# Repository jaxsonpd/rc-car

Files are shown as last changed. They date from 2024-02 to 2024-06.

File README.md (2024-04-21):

Wacky Racers
===============

This contains a directory structure for your assignment.

doc -- documentation

hw  -- hardware (add your schematic PDF here)

src -- source code

Assignment instructions
-----------------------

The [instructions](https://eng-git.canterbury.ac.nz/wacky-racers/wacky-racers/-/raw/master/doc/instructions/instructions.pdf) are in a PDF file stored in this repository (you'll also get a copy when you fork the project).

Assignment guide
----------------

The [guide](https://eng-git.canterbury.ac.nz/wacky-racers/wacky-racers/-/raw/master/doc/guide/guide.pdf) is a PDF file stored in this repository (you'll also get a copy when you fork the project).

C style Guide
-------------

https://github.com/jaxsonpd/etc/blob/main/Guides/C%20Style%20Guide.md

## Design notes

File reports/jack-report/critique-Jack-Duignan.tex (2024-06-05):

\documentclass[a4paper,12pt]{article}
\usepackage{color}

\setlength{\oddsidemargin}{0mm}
\setlength{\evensidemargin}{-14mm}
\setlength{\marginparwidth}{0cm}
\setlength{\marginparsep}{0cm}
\setlength{\topmargin}{2mm}
\setlength{\headheight}{0mm}
\setlength{\headsep}{0cm}
\setlength{\textheight}{240mm}
\setlength{\textwidth}{168mm}
\setlength{\topskip}{0mm}
\setlength{\footskip}{10mm}
\setlength{\parindent}{8ex}

\newcommand{\comment}[1]{\emph{\color{blue}#1}}

\title{ENCE461 Wacky Racers Assignment Critique}
\author{Jack Duignan, Group 33, Hat board}
\date{\today}

\begin{document}
\maketitle

\section{Strengths}

The group 33 wacky hat had three main strengths. First the design of the PCB was very clean with a large number of test-points and no components on the back. This allowed for quick assembly and easy debugging. Second, the board had the ability to be powered from both battery and USB. This was achieved using a header which could be bridged to bypass the H-bridge and supply VBUS directly to the 5V plane. This was extremely useful allowing for testing of the radio without a battery. Third, the software was modularised and well documented allowing both the members of the hat and the car to work on each others problems without much verbal explanation needed.

\section{Weaknesses}

The wacky hat had three weaknesses. First the buzzer was powered off 3V3 without a resister in parallel. This meant that the sound produced was quiet making the song hard to hear. Second, the linear voltage regulators had their bypass pins pulled high which stopped them working correctly luckily these could be pried up from the PCB and the fault was rectified without needing to replace any components. Third the sensitivity of the control system, specifically of the y-axis (turning), was very high making the racer hard to control at slow speeds. This was fixed somewhat in the lead up to the race; however the control system value calculation should have been completely rewritten.

\section{Improvements}

The hat could be improved by: powering the buzzer off 5V with a resistor in series, leaving the 3V3 linear regulators bypass pins floating, and by implementing more gradual sensitivity on the y-axis. These improvements are small things that did not affect the core functionally of the system and where easily rectified. As a whole the system performed well without bugs.

\section{Contribution}

I had four main contributions to the project. First, I created the base schematic used for both the wacky hat and racer which included the SAM4S and radio, GPIO and power supplies. Second, I completed around half of the PCB tracing and layout for the wacky hat. Third I wrote the majority of the software for the wacky hat including the main scheduler, accelerometer interfacing, and the buzzer code. Fourth I completed some debugging of the wacky racer including radio communication and scheduling. I think my contribution was more than others in the team but this was a reflection of the greater amount of spare time that I had when the milestones were due.

\section{Recommendations for future students}

My main recommendation is to start early and leave a large amount of time for the PCB as this is crucial to get right. My team spent a long time on the PCB and schematic design and because of this had to do functionally no rework making the rest of the project much easier. Secondly I would encourage other students to read through the provided libraries as they contain a lot of great examples of well written code and give a good starting point for the software. Finally I would recommend that students design the system with the race in mind with tuning parameters that can be used to change how the controller handles as this will give them a huge advantage in the race.

\section{Recommendations to improve project}

I think that another milestone should be added after radio communication which assess the performance of the racer-hat system. Then the race should be pushed to study leave or everything moved a week forward in the term. I also think that it is imperative that more lab slots are added on another day with the ability for students to ask questions on the first day then be assessed on the second. This is nessasary as the current system does not really allow for any of the actual software design to be completed in the labs. Finally I think that more time needed to be allowed during software development to ensure that the students create clean code that is well modularised. 

\section{Peer assessment}

\noindent
\begin{tabular}{|l|l||l|l|}
\hline
\multicolumn{2}{|c||}{My board} & \multicolumn{2}{c|}{Whole system} \\
\hline
Name \hspace{5cm} & Score     & Name \hspace{5cm} & Score \\
\hline \hline
Jack Duignan        & 3 & Jack Duignan        &  3 \\ \hline
Ethan Wildash-Chan  & 2 & Ethan Wildash-Chan  &  2 \\ \hline
                    & & Isha Patel            &  2 \\ \cline{3-4}
                    & & Daniel Hawes          &  3 \\ \hline
\end{tabular}

\section{Workload}

\noindent
\begin{tabular}
  {|l|l|l|l||
    l|l|l|l||
    l|l|l|l|}
  \hline
  \multicolumn{4}{|c||}{Racer} &
  \multicolumn{4}{|c||}{Hat} &
  \multicolumn{4}{|c|}{System integration}  \\ \hline
    Des & Bld & SW & Test &
    Des & Bld & SW & Test &
    Des & Bld & SW & Test \\ \hline
    4 & 1 & 4 & 4 &
    37 & 7 & 45 & 10 &
    1 & 0 & 10 & 15 \\ \hline
\end{tabular}
\end{document}

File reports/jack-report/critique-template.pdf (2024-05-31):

# ENCE461 Wacky Racers Assignment Critique

### Jack Duignan, Group 33, Hat board

### May 31, 2024

## 1 Strengths

In this section describe what you think are the strengths of your design, PCB layout, and overall wacky racer are.
The group 33 wacky hat had three main strengths. First the design of the PCB was very clean with a large number of testpoints and no components on the back. This allowed for quick assembly and easy debugging as the traces visable. Second, the board had the ability to be powered from both battery and USB. This was achived using a header which could be bridged to bypass the H-bridge and supply VBUS directly to the 5V plane. This was extremly useful allowing for testing of the radio without a battery. Third, the software was modularesed and well documented allowing both the hat and car to work on each others problems without explination needed. This simplified debugging.

## 2 Weaknesses

In this section describe what you think are the weaknesses of your design, PCB layout, and overall wacky racer are.
The wacky hat had three weaknesses. First the buzzer was powered off the 3V3 without a resister in parallel. This meant that the sound produced was quiet and in the end a resistor was soldered across the buzzer terminals. Second, the linear voltage regulators had there bypass pins pulled high which stopped this working luckly these could be pried up from the PCB and the fault was rectified without needing to replace any components. Third the control system spesifically the sensitivity of the y-axis (turning) was very high making the racer hard to control at slow speeds this was mitigated somewhat; however more needed to be done.

## 3 Improvements

In this section describe what you would like to have done differently with the advantage of hind-sight.
The hat could be improved by: powering the buzzer off 5V with a resistor in series, leaving the 3V3 linear regulators bypass pins floating, and by implementing more gradual sensitivity on the y-axis.

## 4 Contribution

In this section describe what you perceive as your contribution to the project compared to the other members of your team.
I had four main contributions to the project. First, I created the base sechematic used for both the wacky hat and racer which included the SAM4S and radio, GPIO and power supplies. Second, I completed around half of the PCB tracing and layout for the wacky hat. Third I wrote the majority of the software for the wacky hat including the main schedular, acceleromiter interfacing, and the buzzer code. Fourth I completed some debugging of the wacky racer including radio comunication and scheduling.

## 5 Recommendations for future students

In this section describe recommendations (with reasons) for future students doing a similar project.
The main recommendation is to start early and leave a large amount of time for the PCB as this is cricual to get right. My team spent a long time on the PCB and schematic design and becouse of that had to do functionally no rework making the rest of the project much easier. Secondly I would incouge other students to read through the provided libraries as they contain a lot of great examples of well writen code and give a good starting point for the software. Finally I would recommend that students design the system with the race in mind with tunning paramiters that can be used to change how the controller handles. As this give them a huge advantage in the race.

## 6 Recommendations to improve project

In this section describe your recommendations (with reasons) for how the project could be improved.
I think that another milestone should be added after radio communication which assess the performance of the racer, hat system. Then the race should be pushed to study leave or everything moved a week forward. Second I think that it is imperitive that more lab slots are added on another day with the ability for students to ask questions of the first day then be assessed on the second. This is nessasary as the current system does not really allow for any of the actual software design to be completed in the labs.

## 7 Peer assessment

There are two assessments to fill into the table:
My board | Whole system
Name | Score | Name | Score
Jack Duignan | 3 | Jack Duignan | 3
Ethan Wildash-Chan | 2 | Ethan Wildash-Chan | 2
| | Isha Patel | 2
| | Daniel Hawes | 3

## 8 Workload

Racer | Hat | System integration
Des | Bld | SW | Test | Des | Bld | SW | Test | Des | Bld | SW | Test
4 | 1 | 4 | 4 | 37 | 7 | 45 | 10 | 1 | 0 | 10 | 15

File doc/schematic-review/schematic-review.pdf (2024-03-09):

# ENCE461 Schematic Review

### M.P. Hayes

Bring your schematics, printed on A3 paper

## 1 Common

1. Student names and group number in title block
2. Battery fusing (this is mandatory)
3. Use serial wire debug interface for programming
4. 3.3 V MCU regulator can be back driven (the CAT6219 can). Others may require a diode
5. Short circuit protection for MCU pio pins going to external headers
6. Battery voltage monitoring
7. The analogue inputs to the MCU do not exceed 3.3 V
8. LEDs for debugging
9. Jumpers for mode configuration (radio channel select)
10. Test points
11. Ground test points
12. USB signals are not swapped
13. USB has series termination resistors (27 ohm)
14. Power supply filtering for radio (recommend ferrite bead or resistor in series with power rail with parallel capacitor)
15. The radio needs to be connected to SPI pins (MISO/PA12, MOSI/PA13, SCK/PA14)
16. Radio IRQ connected to MCU PIO pin
17. Radio uses SPI clock (SCK) not the TWI clock (TWCK)
18. TWI uses TWCK0/PA4 and TWD0/PA3 or TWCK1/PB5 and TWD1/PB4.
19. SAM4S erase pin on testpoint
20. SAM4S has 12 MHz crystal

1

21. Reset button connected to NRST pin
22. Power on/off button connected to WKUPn pin
23. Avoid PB4–PB5 for general I/O (they default to JTAG pins on reset but can be reconfigured in software)
24. Have external pull-down resistors to ensure chips are disabled on power-up
25. Have a few spare PIO pins connected to pads for last minute mods.

## 2 Hat board

1. Drive circuit for piezo tweeter
2. Accelerometer nCS pin connected high to enable I2C operation
3. Pullup resistors on TWI (I2C) bus

## 3 Racer board

1. Can isolate H-bridge and buck regulator with jumper or zero ohm resistors
2. MOSFET(s) for actuator (if use p-channel MOSFET need transistor to provide sufficient gate voltage to turn MOSFET off)
3. H-bridge driven by four PWM signals (it is best to use PWMHx, note PWMLx and PWMHx are complementary)
4. H-bridge AISEN and BISEN pins connected to ground (unless using current control)

2

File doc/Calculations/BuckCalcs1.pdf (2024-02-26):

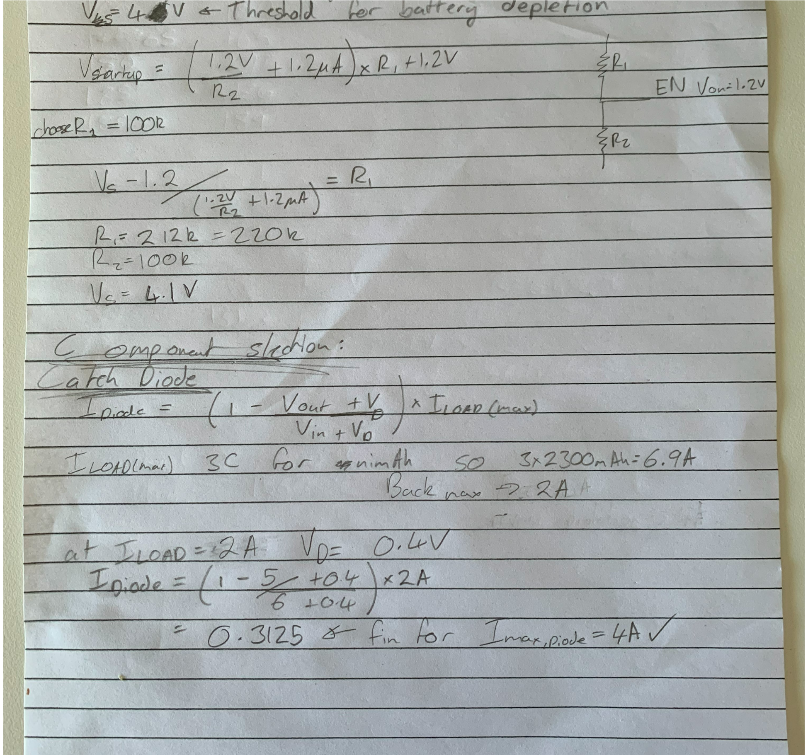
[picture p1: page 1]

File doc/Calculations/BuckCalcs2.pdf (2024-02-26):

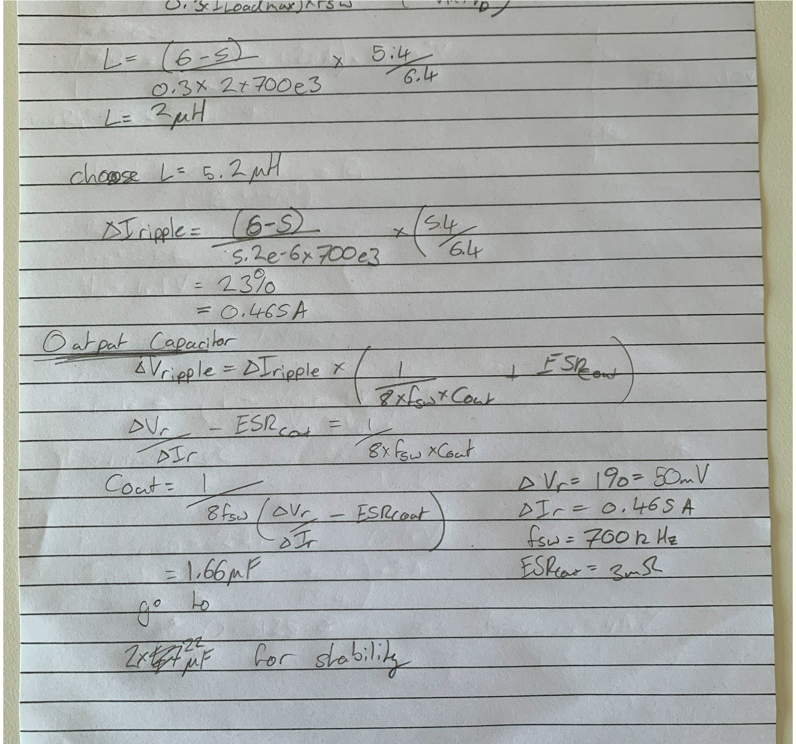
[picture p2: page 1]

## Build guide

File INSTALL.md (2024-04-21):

# Install

This document details the installation process for the toolchain on wsl

# Installing WSL

Source: https://learn.microsoft.com/en-us/windows/wsl/install

Open a powershell prompt as an admimastrator and run:

```
wsl --install
```
This installs ubuntu.

Restart the terminal and now ubuntu should be in the drop down. Let it install then set user name and password.

Once this is completed you can then ensure it is up to date using:

```
sudo apt update && sudo apt upgrade
```

# USB pass through

Source: https://learn.microsoft.com/en-us/windows/wsl/connect-usb

1. Install usbipd (download the msi)
2. Attach usb device to the windows machine
3. Run 
```
usbipd list
```
to list comands
4. bind the usb device that should be shared (this makes it available to wsl)
```
usbipd bind --busid 4-4
```
5. Attach the usb device to wsl
```
usbipd attach --wsl --busid <busid>
```
6. Then use:
```
lsusb
```
To list the devices attached to the ubuntu installation

# Toolchain

The toolchain can then be downloaded using the guide found at:

https://eng-git.canterbury.ac.nz/wacky-racers/wacky-racers/-/raw/master/doc/guide/guide.pdf?inline=true

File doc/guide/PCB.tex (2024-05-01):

\chapter{PCB layout}

Before you lay out your PCB, an hour spent checking your schematic
will avoid many hours of testing and rework grief!  I annotate a
printed schematic with a highlighter to ensure I have considered
everything.

Laying out a PCB is a topological puzzle.  Note only do you need to
connect all the components, you need to consider:
%
\begin{enumerate}
\item Signal integrity

\item Manufacturability

\item Testability

\item Thermal issues
\end{enumerate}

\section{Altium tutorial}

The Altium tutorial for creating a PCB can be found on the ENCE461
Learn page.

\label{pcb-recommendations}

\section{Placement}
\label{placement}

\begin{enumerate}
\item
  Keep small signal analogue components (radio) well away from digital
  electronics and power electronics.
\item
  Place local decoupling capacitors close to MCU to minimise the loop area.
\item
  Place bulk capacitors close to where power comes from.
\item
  Keep the crystal close to the MCU.
\item
  Place switches so they can be pushed.
\item
  Place LEDs so they can be seen.
\item
  Place USB connector so it can be connected to.
\item
  Place connectors on edge of PCB with wires going away from the board.
\end{enumerate}

\section{Power supplies}

The goal of routing power supplies is to reduce impedance (both
resistive and inductive).

\begin{enumerate}

\item Use planes for power distribution.

\item Use separate vias for every power and ground connection.

\item If cannot use power plane for power connection, make trace as
  wide\footnote{To reduce inductance and resistance.} as possible.

\item Do not put splits in planes\footnote{Unless you know what you
  are doing.}.

\item Keep planes away from the radio antenna; otherwise the radio
  range is limited.

\item Before `pouring' a polygon to create a power or ground plane
  connect the nets with traces and vias.
\end{enumerate}

\section{Signal traces}

The goal of routing signal traces is to reduce crosstalk to improve
signal integrity.  You should always consider the return current path;
this will take the path of least impedance.

% https://resources.altium.com/p/differential-pair-impedance-using-calculator-design-your-pcb

% https://resources.altium.com/p/differential-microstrip-impedance-calculator

\begin{enumerate}

\item First, route differential signal traces as a pair (e.g., USB) on
  top layer (to form microstrips with the ground
  plane)\footnote{Ideally, the differential characteristic impedance
    should be 90 ohms.  This depends on the trace width, trace
    separation, trace thickness, and height of the traces above the
    ground plane.  If you are keen see \url{
 https://resources.altium.com/p/differential-microstrip-impedance-calculator}.}.

\item Route high-speed (above 50\,kHz, e.g., SPI, I2C) signal traces
  on the top layer (to form a microstrip with the ground plane).
  These traces can be thin\footnote{The trace width affects the
    characteristic impedance of the microstrip but this is not an
    issue for the small boards used for the assignment.}, say
  0.3\,mm\footnote{The manufacturer can produce 0.15\,mm traces but
    the Altium design rules for this assignment set a minimum width of
    0.2\,mm to be safe.}.

\item Keep a high-speed trace well away from any other trace to reduce
  crosstalk (see the 3-W rule).

\item Avoid high-speed signal traces jumping layers\footnote{This
  makes the return current take a tortuous path, increasing
  crosstalk.}.  If you have to, use vias close to the ends of traces
  and run the traces on the bottom layer (to form a microstrip with
  the power plane).  Be careful not to route traces on the bottom
  layer over gaps in the power plane (this breaks the microstrip and
  thus increases crosstalk) \footnote{See \url{https://www.signalintegrityjournal.com/articles/692-split-planes-and-what-happens-when-microstrip-signals-cross-them}.}.

\item Route low-level analogue signals well away from the high-speed
  traces, preferably on the bottom layer (where they are shielded from
  the high-speed traces).

\item Use thick, short traces for high current signals (e.g., motor)
  to reduce resistance.

\item Finally, route the low-speed signal traces (for LEDs and buttons
  etc.).  These can jump layers to go around the high-speed traces.

\end{enumerate}

In the past it was undesirable to have acute angles ($<90^{\circ}$) in
traces due prevent the formation of acid traps during etching.
However, it seems that modern PCB etching does not have this
problem\footnote{\url{https://resources.pcb.cadence.com/blog/are-acid-traps-still-a-problem-for-pcbs-in-2019-2}}.

\section{Vias}

\begin{enumerate}
\item Use normal vias but not blind or buried vias.  The smallest via
  that can be made for this assignment has a 0.3\,mm hole with a
  0.8\,mm annulus.  However, it is better to use a via with a 0.5\,mm
  hole and 1.0\,mm annulus.

\item If you use a via underneath a component with a metal heatsink
  pad, ensure it is tented (these have a layer of insulating solder
  resist).  Note, untented vias are useful for test points.
\end{enumerate}

\section{Recommended layouts}

For any switching power supply, sensitive analogue, or BGA fanout, the
chip manufacturer usually provides a recommended layout.

\section{Check list}
\label{PCB-check-list}

\begin{enumerate}
\item Check your schematic.  Then get someone else to check your
  schematic.  Query every component.

\item Perform a DRC (Design Rule Check)] using Altium.

\item Add PCB test points, test points, and more test points.  You
  will need one for every signal and power supply.  \textbf{You have
    been warned!}  If you don't believe me, compare the size of an
  oscilloscope probe to a surface mount IC pin and see if you can hold
  the probe in place.  I recommend using 1206 test points since the
  smaller ones rip off easily.

    

\item Label the test points on the silk screen with meaningful names.

\item Add ground test points that you can clip an oscilloscope ground
  lead to.  Keep these away from other test points to avoid shorting
  with the oscilloscope ground clip.  I recommend making a
  staple-shaped wire loop, soldered between two holes.



\item Check mounting holes.

\item Check component footprints, especially connectors, voltage
  regulators, and surface mount transistors by placing the parts on a
  print-out of the PCB design.

\item Ensure that power supply traces are wide as possible, preferably
  planes, to reduce their inductance.

\item Ensure that high current traces are wide as possible to reduce
  their resistance.

\item Do not connect IC pins directly between the pads since it is not
  possible to tell if a solder blob is accidental or deliberate.

\item Insert vias to ground plane to ensure that all parts are
  connected.  Do not leave unconnected copper.

%\item If not using plated through vias do not place vias under
%  components.

\item If placing vias under components with exposed metal pads, make
  sure the vias are ``tented'' (covered in solder mask) to prevent
  unexpected shorts.

\item Stitch power or ground planes where vias or traces cut them up.

\item Traces of width $W$ should be separated by at least $2W$ to
  reduce crosstalk.  This is the 3-W rule since the trace centres are
  $3W$.  An exception is for differential signals; these should be
  routed close together with a uniform spacing.

\item Do not run a microstrip traces right on the edge of the PCB.  If
  trace is of width $W$ it should be at least a distance $W$ from the
  edge to reduce electric field fringing effects.

\item Use large traces for pads on connectors that may be subject to
  mechanical forces (power jacks, pluggable terminals, etc.) to
  prevent trace cracking.

\item If you have high voltages check clearances.

\item Check pad to trace clearances to avoid potential solder bridges.

% \item Check that it is possible to top-solder through-hole components
%  on non-plated-through boards.

\item Ensure like signals are grouped, data lines, address lines, control lines, analogue signals, etc.

\item Check the thermal path for parts that get hot.

\item Run traces over reference (power or ground) planes to create a
  microstrip trace; avoid traces running over cuts in a reference
  plane.

\item Check that hole diameters are larger than the pin diameters for
  connectors and through hole. 25\% over the lead diameters is
  typical.  Remember to look at the diagonal dimension for square pins
  or your holes may be too small.

\item Check the drill file report to make sure the hole sizes are what
  you would expect. There should be no holes with sizes of zero, no
  weird sizes, no super large sizes unless required by the design.

\item Check that connections of thermal vias have clearance to other
  traces and pads.

\item Pay close attention to clearances on internal planes of
  multilayer boards; shorts on these planes can only be removed with
  precision drilling.

\item Number pins on connectors, big ICs, selection jumpers, etc. For
  connectors, number enough pins so that the pin ordering is
  obvious.  For large ICs consider adding tickmarks every 5 pins.

\item Make the pad for pin 1 of every IC square. Also consider putting
  a silkscreen dot next to pin 1.

\item Leave at least 20--50\,mils (0.5--1.3\,mm) clearance between
  components and the edge of the board. This makes it less likely that
  inaccuracies in board fabrication will cause part of a pad to get
  chopped off.

\item Check for component clearances from enclosure including heights.

\item Look at each net individually to ensure that it does not take an
  overly long path around the board. Many layout tools have a
  highlight net feature that makes this a fast process.

\item Do not let the silkscreen overlap pads. Try to avoid having
  silkscreen overlapping via holes or areas of the board that will be
  routed away (large holes, slots, tabs, etc.), since legibility will
  be poor.

% \item If ICs are being soldered with solder paste ensure that there is
%  a solder mask between pads.
 \end{enumerate}

\section{Design rule checks}

This section considers common Altium design rule violations.  For more
information see the Altium wiki.

\subsection{PCB manufacture violations}

You do not want any of these.  If a trace is too thin then etching may
produce a hole in it.  It two traces are too close together, they may
end up joined.

\subsection{PCB assembly violations}

If you want to make thousands of boards, then you want to avoid these
violations.  For a one-off board, they do not matter since you can fix
the faults they may cause with a soldering iron.

\subsubsection{SMD neck-down constraint}

Traces connecting to SMD pads often need to be reduced in thickness to
minimise heat transfer from the SMD pad (unequal PAD temperatures can
lead to component tombstoning or rotation in the oven).  The traces
widths should be a maximum of 50 \% of the width of the pad and should
be of the same size to prevent component movement due to unequal pad
temperatures.  The length of the neck-down can be as short as 0.5\,mm.

This is not so critical for integrated circuits with many pins (except
if a solder mask is not used since solder might flow away from the
pad).

\subsubsection{Silk to solder mask}

Here Altium thinks the silk screen is being printed over a pad; most
manufacturers detect this and delete the offending text.  The downside
is that it might make it hard for you to find a component by name.

\subsubsection{Minimum solder mask sliver constraint}

This occurs with chips having pins that are close together.  It is a
warning that the PCB manufacturer may not be able to make the thin
sliver of solder mask that is applied between pads to reduce the
chances of having a solder blob between the pins.  For a prototype it
is not a concern since the solder blob can be easily removed with a
small soldering iron.

\subsubsection{SMD pad to corner}

This is warning about potential acid traps.  You can ignore
it\footnote{\url{https://resources.pcb.cadence.com/blog/are-acid-traps-still-a-problem-for-pcbs-in-2019-2}}.

\subsection{Signal integrity violations}

These are not showstoppers but are important if you want to sell a
product that meets EMC
regulations\footnote{\url{https://learnemc.com/emc-regulations-and-standards}}.

\subsubsection{SMD pad to plane constraint}

What this means is that you have placed a via to a power or ground
plane too far from a SMD pad.  Simply add another via closer to the
pad.  There is no need to skimp on vias for power supply connections.

This violation indicates you that you are adding unnecessary
inductance by increasing the loop area and thus compromising signal
integrity.

Unfortunately, Altium does not detect when you use a power decoupling
capacitor to mitigate this inductance and thus will report
false-positives.  For some reason, whenever there is a decoupling
capacitor pad between an IC pad and a via to a plane, it cannot
calculate the distance of the trace and reports it as being about
2.3\,m!  So, ignore this error.

The goal is to place the decoupling capacitor to minimise the area of
the loop formed by the current flowing from the capacitor to the IC
power and ground pins.  Multiple vias to power/ground planes should
then be placed on the other side of the capacitor.

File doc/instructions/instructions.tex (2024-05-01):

\documentclass[11pt, a4paper]{article}
\title{Wacky Racers 2024 Instructions}
\author{Michael Hayes}
\date{Version 1.111, \today}

\usepackage[margin=1in]{geometry}
\usepackage{parskip}
\usepackage{float}
\usepackage{todonotes}
\presetkeys{todonotes}{inline}{}
\usepackage{graphicx}
\usepackage[T1]{fontenc}
\usepackage{makecell}
\usepackage[breaklinks=true]{hyperref}
\usepackage{tabularx}
\usepackage{subcaption}
\usepackage{listings}
\usepackage{siunitx}
\usepackage{circuitikz}
\usepackage{tikz}
\usetikzlibrary{arrows}

\newcommand{\code}[1]{\texttt{#1}}

\newcommand{\fredyemail}{\url{mailto:fredy.youssif@canterbury.ac.nz}}
\newcommand{\scottemail}{\url{mailto:scott.lloyd@.canterbury.ac.nz}}
\newcommand{\diegoemail}{\url{mailto:diego.ramirez@canterbury.ac.nz}}

\newcommand{\fredy}{\href{mailto:fredy.youssif@pg.canterbury.ac.nz}{Fredy Youssif}}
\newcommand{\scott}{\href{mailto:scott.lloyd@.canterbury.ac.nz}{Scott Lloyd}}
\newcommand{\diego}{\href{mailto:diego.ramirez@canterbury.ac.nz}{Diego Ramirez}}

\newcommand{\theguide}{\href{https://eng-git.canterbury.ac.nz/wacky-racers/wacky-racers/-/blob/master/doc/guide/guide.pdf}{The Wacky Racers Guide}}

\begin{document}
\maketitle

\section{Introduction}

The purpose of this assignment is to design, build, and program an
embedded system using an ARM microcontroller and surface mount
technology.

The goal for each group of four students is to build a remote
controlled vehicle (the Wacky Racer) and its controller (the Wacky
Hat).  At the conclusion of the assignment there will be a dastardly race!

Each group is comprised of two sub-groups of two students.  One of
these subgroups constructs the Wacky Racer and the other constructs
the Wacky Hat.  You may be asking why is the Wacky Hat called the
Wacky Hat?  Well, a hat that controls a remote vehicle using head
motions is not an ordinary hat!

\section{Requirements}

The following requirements are mandatory if you wish to maximise your
marks.

\subsection{Wacky racer}

\begin{enumerate}
\item The chassis is to be constructed by each group.  These can be 3-D printed,
  constructed from Perspex or wood, etc.  A standard chassis is available from
  the Electronics Lab technician (Diego Ramirez).  The electronics must be
  visible on top of the chassis.  The bumper must be as accessible as the
  the standard chassis.
\item Have a standard working bump sensor (supplied).
\item Locomotion can only use two 6\,V DC motors (supplied).
\item Everything must be powered from a single 5-cell NiMH battery pack (supplied).
\item Use a single four layer printed circuit board of dimension 85\,mm$\times$64\,mm.
\item Use an ARM microcontroller (Atmel SAM4S).
\item Drive the motors using H-bridges (Texas Instruments DRV8833 dual
  H-bridge).
\item Regulate the nominal battery voltage to 5\,V with a buck
  regulator IC (ADP2302ARDZ-50).
\item Be decorated with an LED tape (supplied) controlled by the MCU.
\item Use a USB interface for debugging.
\item Use a serial wire debug interface for MCU programming/debugging.
\item Have adequate battery fusing and reverse polarity protection.
\item Have a pushbutton connected to the MCU to enter and wake from
  low-power mode (optional).
\item Have a red LED to indicate errors.
\item Have a green LED to indicate status.
\item If the battery voltage drops below 5\,V, the red LED should flash and high power draw devices should be disabled.
\item Interface to the Wacky Hat with a Nordic nRF24 SMD radio module
.
%\item Have a mounted RFID card (supplied) that can be read by the Wacky ramps.
\item Have jumpers or switches to select four radio channels.
\item Be humorous.
\end{enumerate}

\hspace{120mm}

Each Wacky Racer can have a dastardly means of hindering another
team's Wacky Racer.  However, you cannot:
%
\begin{itemize}
\item Damage or destroy another Wacky racer (except in the battle royale)
\item Damage the venue
\item Injure a spectator
\item Jam the radio signals
\end{itemize}

\vspace{1cm}

\begin{figure}[h]
    \centering
    \input{racer_top_level.tex}
    \caption{Racer board top level diagram.}
\end{figure}

\vfill\pagebreak

\subsection{Wacky hat}

\begin{enumerate}
\item Construct a Wacky Hat that contains all the electronics.
\item Everything must be powered from a single 5-cell NiMH battery pack (supplied).
\item Have adequate battery fusing and reverse polarity protection.
\item Use a single four layer printed circuit board of dimension 85\,mm$\times$64\,mm.
\item Use an ARM microcontroller (Atmel SAM4S).
\item Regulate the nominal 6\,V battery voltage to 5\,V with a buck
  regulator IC (ADP2302ARDZ-50).
\item Be decorated with an LED tape (supplied) controlled by the MCU.
\item Use an I2C accelerometer (ADXL345) for head motion detection.
\item Use a USB interface for debugging.
\item Use a serial wire debug interface for MCU programming/debugging.
\item Have a pushbutton connected to the MCU to enter and wake from
  low-power mode (optional).
\item If the battery voltage drops below 5\,V, the red LED should flash and high power draw devices should be disabled.
\item Have an active-high red LED to indicate errors.
\item Have an active-high green LED to indicate status.
\item Play sound when the bumper is hit.
\item Interface to the Wacky Racer with a Nordic nRF24 SMD radio module.
\item Have jumpers or switches to select four radio channels.
\item Be humorous.
\end{enumerate}

%\vspace{1cm}

\begin{figure}[h]
  \centering
  \input{hat_top_level.tex}
  \caption{Racer hat top level diagram.}
\end{figure}

\vfill\pagebreak

\section{Assignment schedule}

The planned activities for the timetabled labs in the Embedded Systems
Lab (ESL) are:
%
\begin{flushleft}
  \begin{tabular}{ c l l }
    Week            &  Assistance  &  Assessment \\
    \hline \hline
    T1-1 & Altium tutorial 1 (schematics)  & \\
    T1-2 & Altium help      & \\
    T1-3 & Schematic review & Schematic submission for review (Monday 9am) \\
    T1-4 & Altium tutorial 2 (PCB) &          \\
    T1-5 & Altium help      & PCB submission 1    \\
    T1-6 & Altium help      & PCB submission 2    \\
    \hline
    B-1  & (break)          &                   \\
    B-2  & (break)          &                   \\
    B-3  & (break)          &                   \\
    \hline
    T2-1 & General          &                   \\
    T2-2 & General          & Blinky            \\
    T2-3 & General          & Accelerometer/motors        \\
    T2-4 & General          & Radio control     \\
    T2-5 & General          & Functionality     \\
    T2-6 & Competition      & Competition, critique  \\
  \end{tabular}
\end{flushleft}

Notes:
%
\begin{enumerate}
\item There are two lab streams.  Your group will need to sign up to
  one of the streams.  Choose an odd numbered group for the Wednesday
  1--3 pm stream or an even numbered group for the Wednesday 3--5 pm
  stream.

\item There may be a 6--10 day delay for the PCBs to be manufactured
  from the time of submission.  You will then need to book an assembly
  session in the SMT lab provided you have done the SMT lab induction.

\item Do not underestimate the blinky milestone.  The program is
  trivial; you just have to flash an LED.  However, it requires having
  a functional PCB, a functional toolchain, and the ability to
  download code into the microcontroller's flash memory.

\end{enumerate}

\section{Assessment}

The marks breakdown (max. 0x64) is:
%
\begin{flushleft}
  \begin{tabular}{ll}
    PCB submission & 0--0xa marks\\
    Blinky milestone  & 0x5 marks\\
    Accelerometer/motor milestone  & 0x5 marks\\
    Radio control milestone  & 0x5 marks\\
    Functional assessment & 0--0x14 marks \\
    Board inspection & 0--0x1e marks \\
    Competition & 0--0xa marks \\
    Individual critique & 0--0xf marks \\
  \end{tabular}

\end{flushleft}

\subsection{Milestones}

There are five milestones.  To achieve the associated marks, they must
be demonstrated to a T.A. by the end of the lab for your allotted
stream.  If you need an exception to this, see \fredy\ with a
\emph{very} good reason such as isolating with COVID.  The milestone
requirements are:
%
\begin{description}
\item [Schematic review] Submit your A3 schematic on Learn for
  review.  Lose 10 marks if you miss the submission time.

\item [PCB submission] Submit your PCB design to Learn for
  manufacture.  To encourage early submission there is a sliding scale
  for marks depending on when the PCB is submitted, see table.  After
  week 6, there is a 10 mark penalty per week.  \textbf{NB, a rushed
    PCB design will cause you more grief, more PCB rework, and a lower
    mark for the inspection.}

  It is not possible for me to cover all aspects of PCB design before
  your PCB submission.  I recommend you read the lecture notes for
  power supply decoupling and crosstalk.

  \begin{tabular}{llll}
    Week & Submission day & Cut-off time  & Mark \\ \hline
    5    & Monday       & 1.00 pm & 10 \\
    5    & Tuesday      & 1.00 pm & 9 \\
    5    & Wednesday    & 1.00 pm & 8 \\
    5    & Thursday     & 1.00 pm & 7 \\
    5    & Friday       & 1.00 pm & 6 \\
    6    & Monday       & 1.00 pm & 5 \\
    6    & Tuesday      & 1.00 pm & 4 \\
    6    & Wednesday    & 1.00 pm & 3 \\
    6    & Thursday     & 1.00 pm & 2 \\
    6    & Friday       & 1.00 pm & 1  \\
  \end{tabular}

\item [Blinky] Demonstrate that can blink an LED controlled by the SAM4S.

\item [Accelerometer/motors]
  For the Wacky Hat,
  \begin{itemize}
  \item Demonstrate the output of accelerometer readings to a PC using USB CDC (as provided in the test apps).
  \item Map the accelerometer readings to two duty cycles for variable speed and steering control (forward and backward), and output the result to a PC using USB CDC.
  \end{itemize}

  For the Wacky Racer,
  \begin{itemize}
    \item Demonstrate the operation of the locomotion motors using PWM signals (as provided in the test apps).
    \item Provide variable speed and steering control for the locomotion motors (forward and backward) from a PC using USB CDC. 
    \end{itemize}

\item[Radio control]

  Demonstrate sending commands from the Wacky Hat to the Wacky Racer
  and vice-versa over a radio link.

%  Demonstrate sending commands from the Wacky Hat to the Wacky Racer
%  over a radio link.
\end{description}

\textbf{If you cannot show the functionality of a previous milestone
  during any assessment, you will fail that assessment and lose any
  marks from the previous milestone.}

\subsection{Functionality assessment}

Functionality requirements:
%
\begin{flushleft}
  \begin{tabular}{l|l}
    Wacky racer & Wacky hat \\ \hline \hline
    Blink LED                      & Blink LED \\
    Drives LED tape                & Drives LED tape \\
    Drive motors forward/backward  & Read from accelerometer \\
    Speed control of motors        & Determine speed from accelerometer \\
    Steering control               & Determine steering from accelerometer\\
    Receive/send radio message     & Receive/send radio message \\
    Jumper selectable radio channel & Jumper selectable radio channel  \\
    Dies on bump                   & Plays sound on bump \\
    Low voltage indication         & Low voltage indication \\
  \end{tabular}
\end{flushleft}
%
Marks are allocated on how well things work.  Up to 5 bonus marks can
be awarded for extra functionality such as:
%
\begin{flushleft}
  \begin{tabular}{l|l}
    Wacky racer                & Wacky hat \\ \hline \hline
    Dastardly stuff            & Plays interesting sounds \\
    Sleep mode                 & Sleep mode \\
  \end{tabular}
\end{flushleft}

Sleep mode is where you shutdown the MCU to save energy and use a
pushbutton to awake the MCU via an interrupt.  Is is easy to get wrong
and hard to save every microamp.

\subsection{Competition}

The competition is a race around an obstacle course.  Marks will be
awarded every time you pass over a Wacky Ramp in the correct order.

%These ramps have an RFID card reader that will detect your Racer if
%you have correctly fitted an RFID card.  The Wacky Ramps change colour
%when they detect a Wacky Racer.

To be awarded any marks for the race:
%
\begin{enumerate}
\item Your vehicle must stop for at least 5\,s if the bumper is hit.

\item Your vehicle must be controlled by motions of the Wacky hat
  sitting on someone's head.
\end{enumerate}

After the races, there will be a battle royale where the last
operational wacky racer wins.  Hitting the bumper of an opponents
wacky racer removes them from the battle.

Marks will also be awarded for wackiness, group costumes, etc.

\subsection{PCB inspection}

This is assessed after the competition.  The categories are:
%
\begin{enumerate}
\item Layout (component placement etc.)
\item Construction (tidiness, rework, etc.)
\item Testability
\item Power supplies (routing, decoupling, etc.)
\end{enumerate}

\vfill\pagebreak
\section{Schedule}

\begin{description}
\item [Week~1]\mbox{}\\[-0.4cm]

  \begin{itemize}
  \item Form a group of four and register your group on Learn.  If you
    cannot form a group of 4, contact \fredy.

  \item Read the Requirements section in this document.

  \item Read the System Design section in the \theguide.

  \item Attempt Altium schematic tutorial.

  \end{itemize}

\item [Week~2]\mbox{}\\[-0.4cm]

  \begin{itemize}
  \item Peruse the datasheets of the key components.

  \item Start your schematic design.

  \end{itemize}

\item [Week~3]\mbox{}\\[-0.4cm]

  \begin{itemize}

    %  \item Sign-up for a SMT lab induction
  \item Submit your Altium schematic for review.

  \item Watch review feedback session.

  \item Correct your schematic.

  \end{itemize}

\item [Week~4]\mbox{}\\[-0.4cm]

  \begin{itemize}
  \item Attempt Altium PCB tutorial.

  \item Start your PCB layout.
  \end{itemize}

\item [Week~5]\mbox{}\\[-0.4cm]

  \begin{itemize}
  \item Submit PCB design (early round).
  \end{itemize}

\item [Week~6]\mbox{}\\[-0.4cm]

  \begin{itemize}
  \item Submit PCB design (late round).
  \end{itemize}

\item [Break]\mbox{}\\[-0.4cm]

  \begin{itemize}
  \item Watch SMT lab induction video.
  \item Populate and test PCB.
  \end{itemize}

\item [Week-7]\mbox{}\\[-0.4cm]

  \begin{itemize}
  \item Demonstrate blinky program if ready.
  \end{itemize}

\item [Week~8]\mbox{}\\[-0.4cm]

  \begin{itemize}
  \item Demonstrate blinky program.
  \end{itemize}

\item [Week~9]\mbox{}\\[-0.4cm]

  \begin{itemize}
  \item Demonstrate accelerometer/motors functionality.
  \end{itemize}

\item [Week~10]\mbox{}\\[-0.4cm]

  \begin{itemize}
  \item Demonstrate radio control.

  \item Plan your costumes!
  \end{itemize}

\item [Week~11]\mbox{}\\[-0.4cm]

  \begin{itemize}
  \item Demonstrate full functionality.

  \item Prepare your costumes and dastardly stuff!
  \end{itemize}

\item [Week~12]\mbox{}\\[-0.4cm]

  \begin{itemize}
  \item Practice control of your wacky racer.
  \item Attend wacky race.
  \item Submit PCB for inspection (box in SMT lab).
  \item Return chassis, batteries, and ST-link programmers.
  \item Submit individual critique to Learn.
  \end{itemize}

\end{description}

\section{Technical stuff}

Read this section carefully.  There are clues as to how we mark your PCBs.

\subsection{Version control}

Use version control for everything, or else!  Learning git is
frustrating but is a skill you will not regret, see \theguide\ for
details.

Your group leader should create a forked copy of the wacky-racers git project
and then add the other group members to the project.  This can be done by:

\begin{enumerate}
\item Go to \url{https://eng-git.canterbury.ac.nz/wacky-racers/wacky-racers}

\item Click `Fork' button.  This will create a copy of the main repository for the project.

\item Click on the `Settings' menu then click the `Expand' button for
`Sharing and permissions'.  Change `Project Visibility' to `Private'.

\item Click on the `Members' menu and add group members as Developers.

\item Using a bash terminal (or other useful shell), enter the command:

\lstset{language=bash}
\lstset{basicstyle=\ttfamily\small}
\lstset{keywordstyle=\color{black}\ttfamily}
\lstset{breaklines}

\begin{lstlisting}
  $ git clone https://eng-git.canterbury.ac.nz/your-userid/wacky-racers.git
\end{lstlisting}

If you do not want to have to enter your password for every git
push/pull operation, you should set up ssh-keys and use the git URL instead:

\begin{lstlisting}[breaklines]
  $ git clone git@eng-git.canterbury.ac.nz:your-userid/wacky-racers.git
\end{lstlisting}

\item Add a remote URL for the main repository.
%
\begin{lstlisting}[breaklines]
  $ cd wacky-racers
  $ git remote add upstream https://eng-git.canterbury.ac.nz/wacky-racers/wacky-racers.git
\end{lstlisting}
%
Again if you do not want to manually enter your password, you can use:
%
\begin{lstlisting}[breaklines]
  $ cd wacky-racers
  $ git remote add upstream git@eng-git.canterbury.ac.nz:wacky-racers/wacky-racers.git
\end{lstlisting}

\item If we add more demo code or tweak the instructions in the main
repository, you can get the updated stuff using:
%
\begin{lstlisting}[breaklines]
  $ git pull upstream master
\end{lstlisting}
\end{enumerate}

\subsection{Schematics}

\begin{enumerate}
\item Attempt the Altium tutorial on Learn.

\item Read the \theguide.

\item Add your name, your partner's name, and your group number to the
  title block.

\item Save PDF files of your schematics in your source repository.
  \textbf{Note, when debugging your PCBs, we will not help you until
    you show us your printed A3 schematic}.

\item I bet that you will not have enough test points to clip an
  oscilloscope probe to.  Do not think you can hold the probe tip
  against an MCU pin without shorting something.  Ensure you give a
  meaningful name to the test point in its comment field.

    

\item Ground test points are essential for an oscilloscope earth clip.
  A U-shaped piece of wire soldered between two holes is good for this.
  Keep ground test points clear of other test points since the earth
  clip may short between them.  You will probably require at least two
  ground points on opposite sides of the PCB.



\item Checking the schematic is the most crucial part of the
  assignment.  If the schematic is wrong then your PCB will be wrong
  and you will need to do rework.  So, schematics must be thoroughly
  checked by another person.

\item It would be useful to have jumpers connected to PIO pins so
  that you can configure your board.



\item In case you forget something, I suggest running some spare PIO
  pins from the MCU to some pads or a connector.

\end{enumerate}

\subsection{PCBs}

\begin{enumerate}
\item Your four-layer PCBs are going to be manufactured in batches.
  There is at least a week turnaround time to get the boards made.

\item It is important that you check footprints for parts they you
  create.  We will impose a 10\% penalty for each rerun of a PCB, say
  due to a footprint mistake.  Get your partner to check.

\item In Altium, turn off the test point designators and turn on
  comments instead. This lets you give them human readable names to
  make your lives easier.

\item PCB layouts must be thoroughly checked by another person.

\item A PCB track can blow faster than a fuse. So keep high current
  tracks fat and short.

\item Clearly mark the positive and negative battery connections on
  the silk screen.

\item Some of the chips can get hot so thermal considerations are
  required.  Follow the manufacturers' guidelines in the datasheets.

\item The switching regulators can interfere with the radios.

\item Use a design rule check to see if any of the following
  constraints are violated:
%
\begin{itemize}
\item Minimum trace width (0.15\,mm)
\item Minimum trace clearance (0.15\,mm)
\item Minimum via size (0.3\,mm hole, 0.6\,mm outer diameter)
\item Minimum hole size (0.3\,mm)
\item Minimum annular ring (0.1\,mm)
\end{itemize}
%
For every violation of one these rules, we will deduct 1\% from your
final mark.

\item Check the checklist in the \theguide\ before submission.
\end{enumerate}

\subsection{Assembly}

\begin{enumerate}
\item Finding shorts is extremely frustrating so maximise clearances
  and test for shorts before populating components.

\item Components can be put through the oven on the reverse side
  although heavy components may need to be glued.

\item Never assume where pin 1 is on an IC; check the datasheet.
  5--10\% of groups will get this wrong.

\end{enumerate}

\subsection{Software}

\begin{enumerate}
\item Read the \theguide.

\item If you are not using version control, you are foolish.

\item Inspect the sample code in the \code{test-apps} directory.

\item If you are trying to program the SAM4S for the first time and
  are feeling tired or impatient, then do something else.
\end{enumerate}

\subsection{Debugging}

\begin{enumerate}
\item Start running small programs (such as the provided demo
  programs) to test each feature separately.

\item An oscilloscope is your friend.  Use normal mode for digital
  signals.

\item It is possible to use the GDB debugger but you need to know what
  you are doing, especially with optimised code (ask the TAs).

\item Drawing a diagram of what you think is happening is highly
  recommended. A simple circuit diagram or timing diagram will often
  help you realise what you have missed and let you fix it without
  asking for help.

\end{enumerate}

\subsection{Possibly asked questions with answers}

\begin{itemize}
\item \emph{Why use the SAM4s MCU?}  For this application most MCUs
  would suffice, even an 8-bit AVR microcontroller.  To level the
  playing field, I have chosen a MCU most students would not have used
  before.  This is an ARM based MCU made by Atmel I have used this in
  a number of projects.  Indeed we used to teach this chip in ENCE361.
  There are many other similar MCUs made by different manufacturers
  such as the STM32 that would just as suitable.

\item \emph{Why use a four layer PCB?}  Come to lectures to find out!

\item \emph{Why use 7.2\,V NiMH batteries for the Wacky Racers?}
  These were a legacy of previous Wacky Racers.  They are also safer
  than lithium batteries with sleep-deprived students.

%% \item \emph{Why can't I program my device using Windows?} Due to
%%   various aspects of the Windows ecosystem, setting up a fully
%%   functional build environment is more complicated, will often vary
%%   from machine to machine, will often break filepaths, and will often
%%   cause bizarre compilation errors. Use at your own risk, we will not
%%   assist in debugging issues related to Windows.

\end{itemize}

\section{Assistance}

\fredy\ is our senior tutor for embedded systems and is in charge of
the assignment.  He is supported by a team of TAs and technicians
\scott\ (\scottemail) and \diego\ (\diegoemail).  \scott\ has his
office in the Surface Mount Lab on Level 2; \diego\ has his office in
the Electronics Lab on Level 2.

\begin{itemize}
\item Emails to the lecturers (except of a personal nature) will be
  quietly ignored.

\item If you have a generic question, please use the ENCE461 Learn
  discussion page.  Note, under the advanced options you can send your
  post without a 30\,minute delay.

\item All decisions regarding legality of your racer and dastardly
  devices are at the whim of \fredy.  Email \fredy\ if you wish to
  keep your ideas secret.

\item TAs will be available in the scheduled lab times.  Priority will
  be given to groups assigned to the current lab session. \textbf{We
    will only provide assistance to students who have a printed A3
    schematic sheet in front of them and have already tried looking up
    the problem in the \theguide.}

\item For questions pertaining to Altium, surface mount assembly, and
  surface mount rework, see \scott\ (SMT Lab technician) and
  \diego\ (Electronics Lab technician).

\item Michael Hayes is really busy pulling all the strings behind the
  scenes and so will only help with gnarly problems referred to by
  \fredy.

\end{itemize}

\section{Student recommendations}

Here are some recommendations from previous years' students:
%
\begin{enumerate}
\item Spend more time on schematic/PCB as it will save a lot of rework time later on

\item Read datasheets well in the design phase

\item Finish milestones early so you can leave the lab session to ask questions about the next milestone

\item Review each other’s boards

\item Write milestone code with the next milestones in mind to avoid rewriting each time
\end{enumerate}

\section{COVID}

\begin{itemize}
\item Some of the lab sessions may need to be held online.

\item The first term does not need lab access, however, you will need
  to be able to run Altium remotely or run the free student-edition of
  Altium.  The instructions and files can be found on the ENCE461
  Learn page.

\item If because of illness or isolation your group cannot meet a
  milestone, email \fredy.

\item Some of the milestones may need to be altered.

\end{itemize}

\end{document}

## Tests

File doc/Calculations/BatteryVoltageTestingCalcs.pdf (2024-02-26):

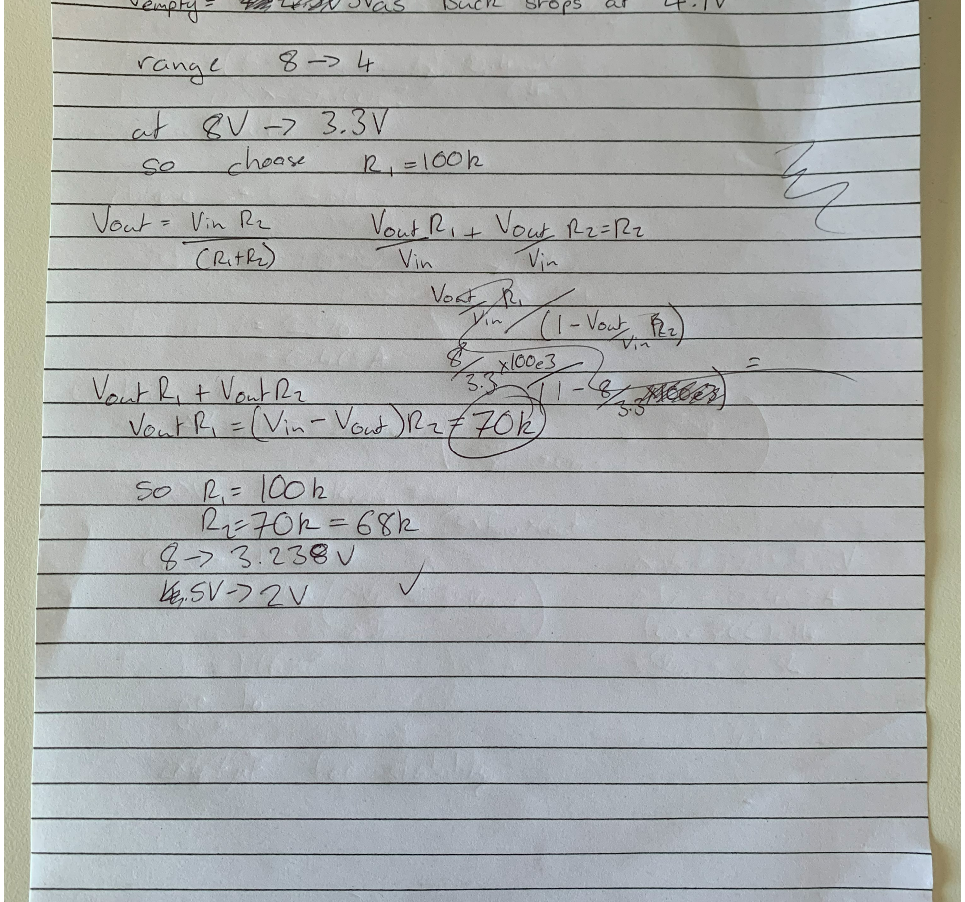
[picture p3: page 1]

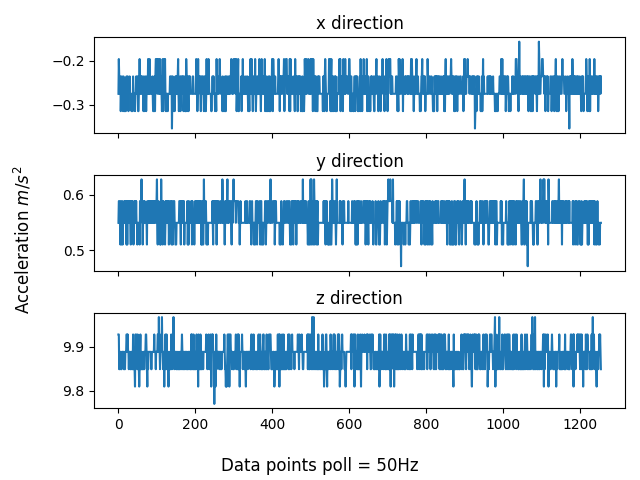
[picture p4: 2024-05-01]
testing/figs/stationary_raw.png

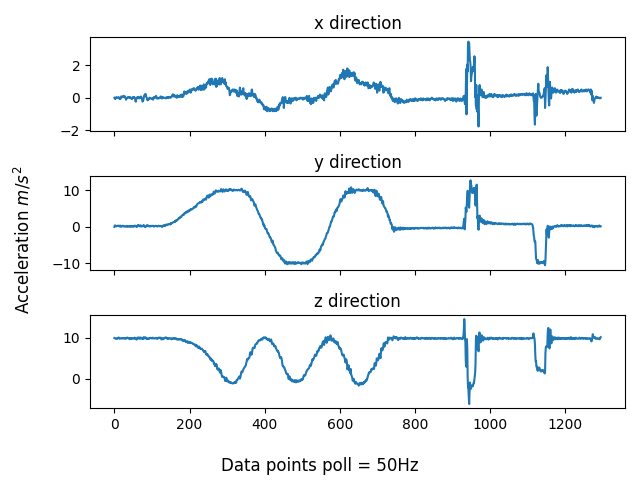
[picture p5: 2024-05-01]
testing/figs/yroll_raw.png

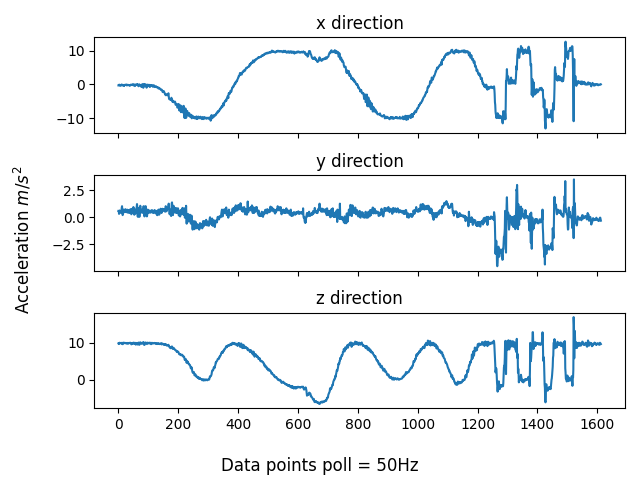
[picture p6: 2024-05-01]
testing/figs/xroll_raw.png

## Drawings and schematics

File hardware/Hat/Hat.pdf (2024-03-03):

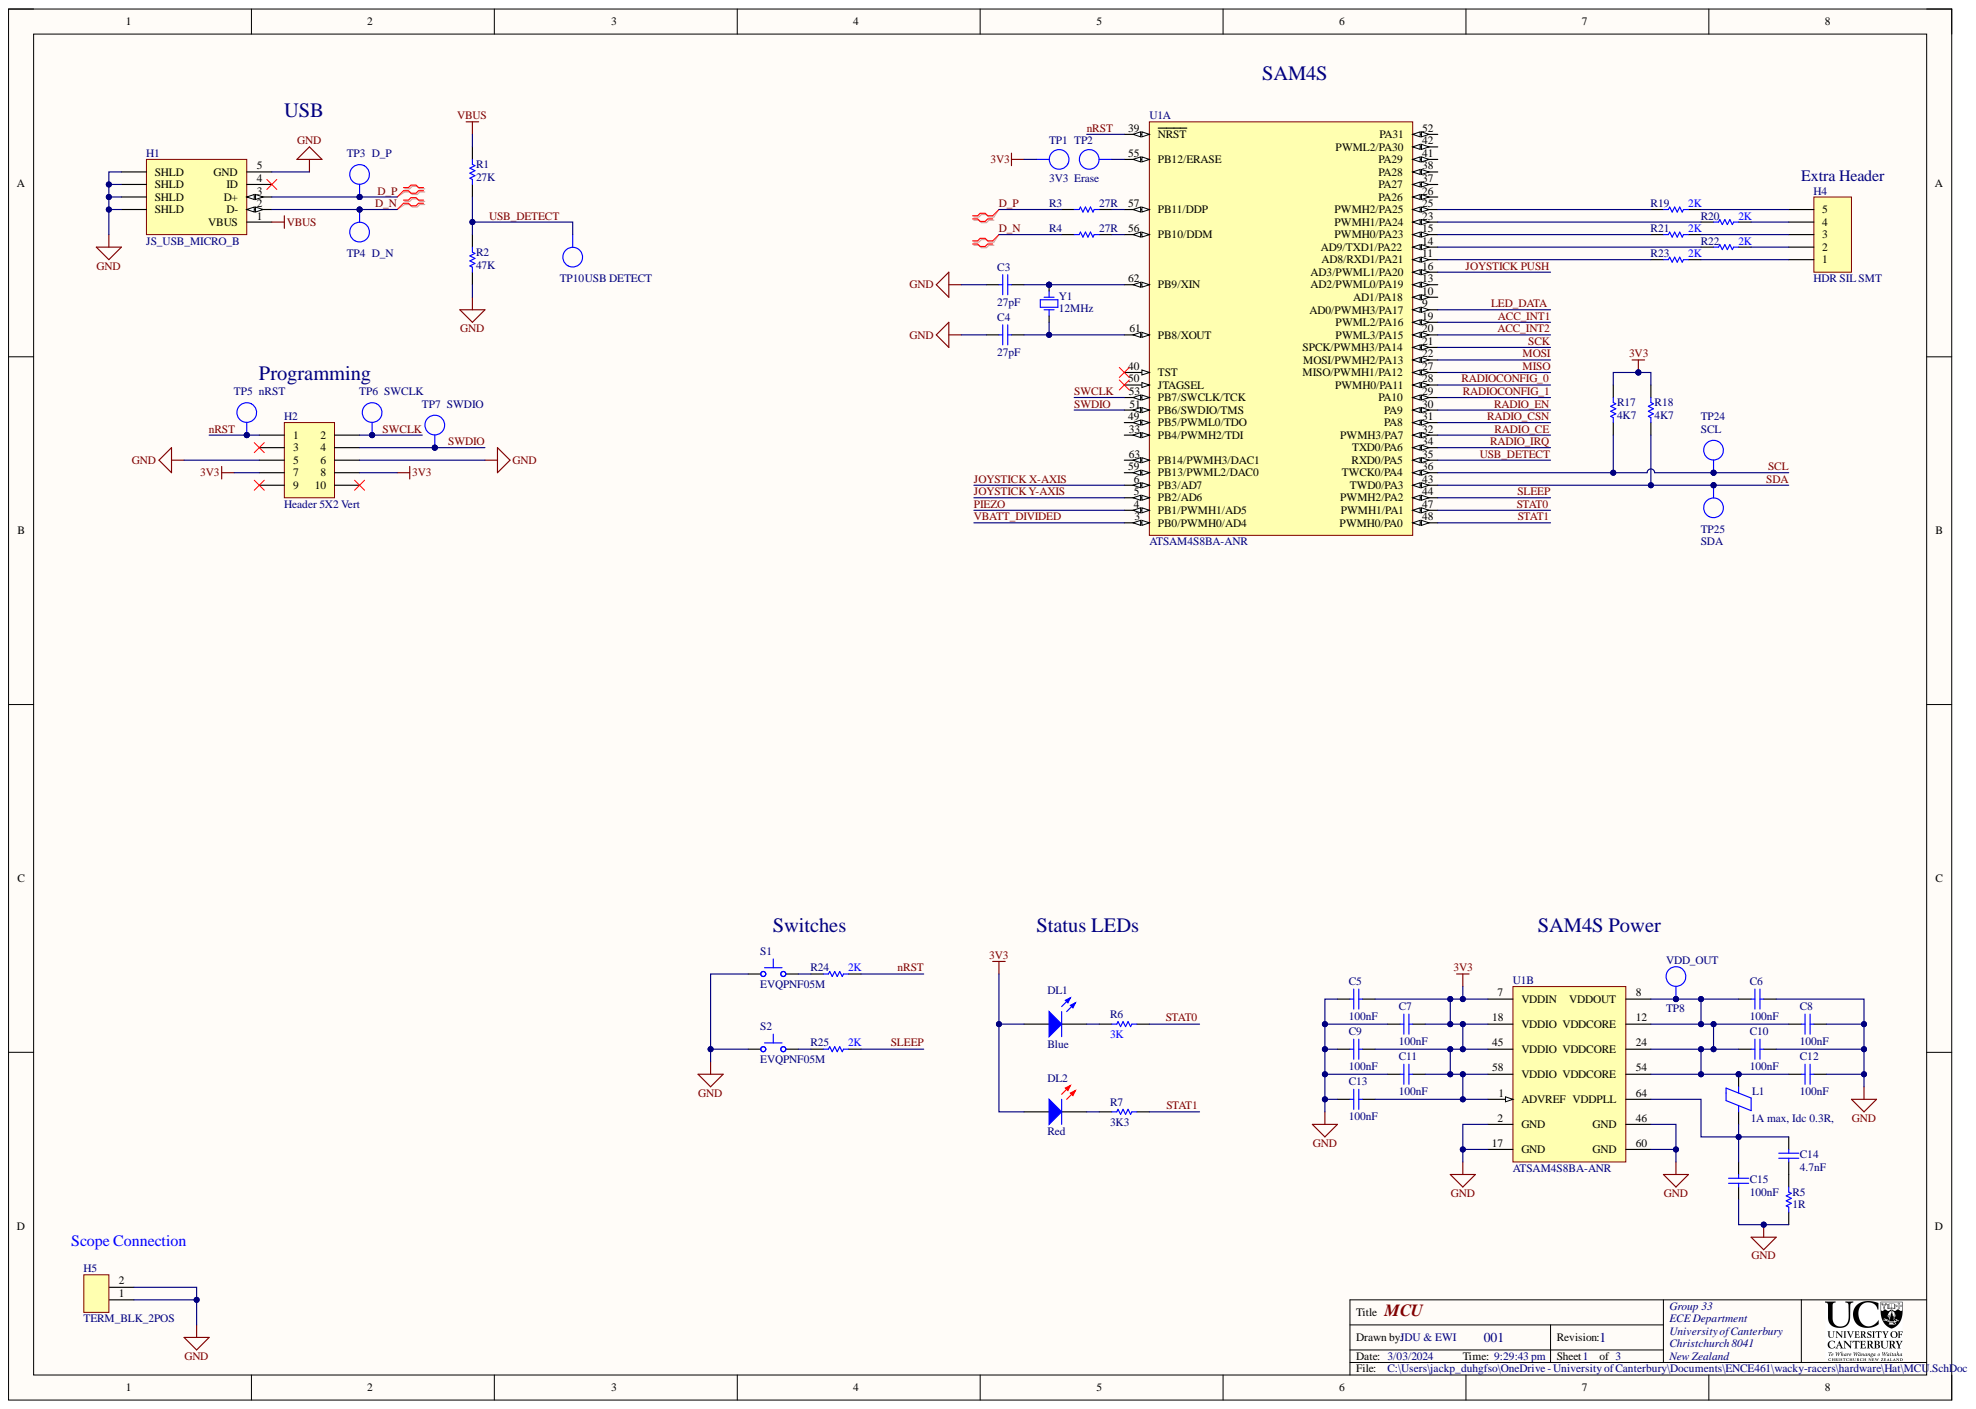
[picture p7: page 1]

Drawn by:
C:\Users\jackp_duhgfso\OneDrive - University ofCanterbury\Documents\ENCE461\wacky-racers\hardware\Hat\MCU.SchDoc

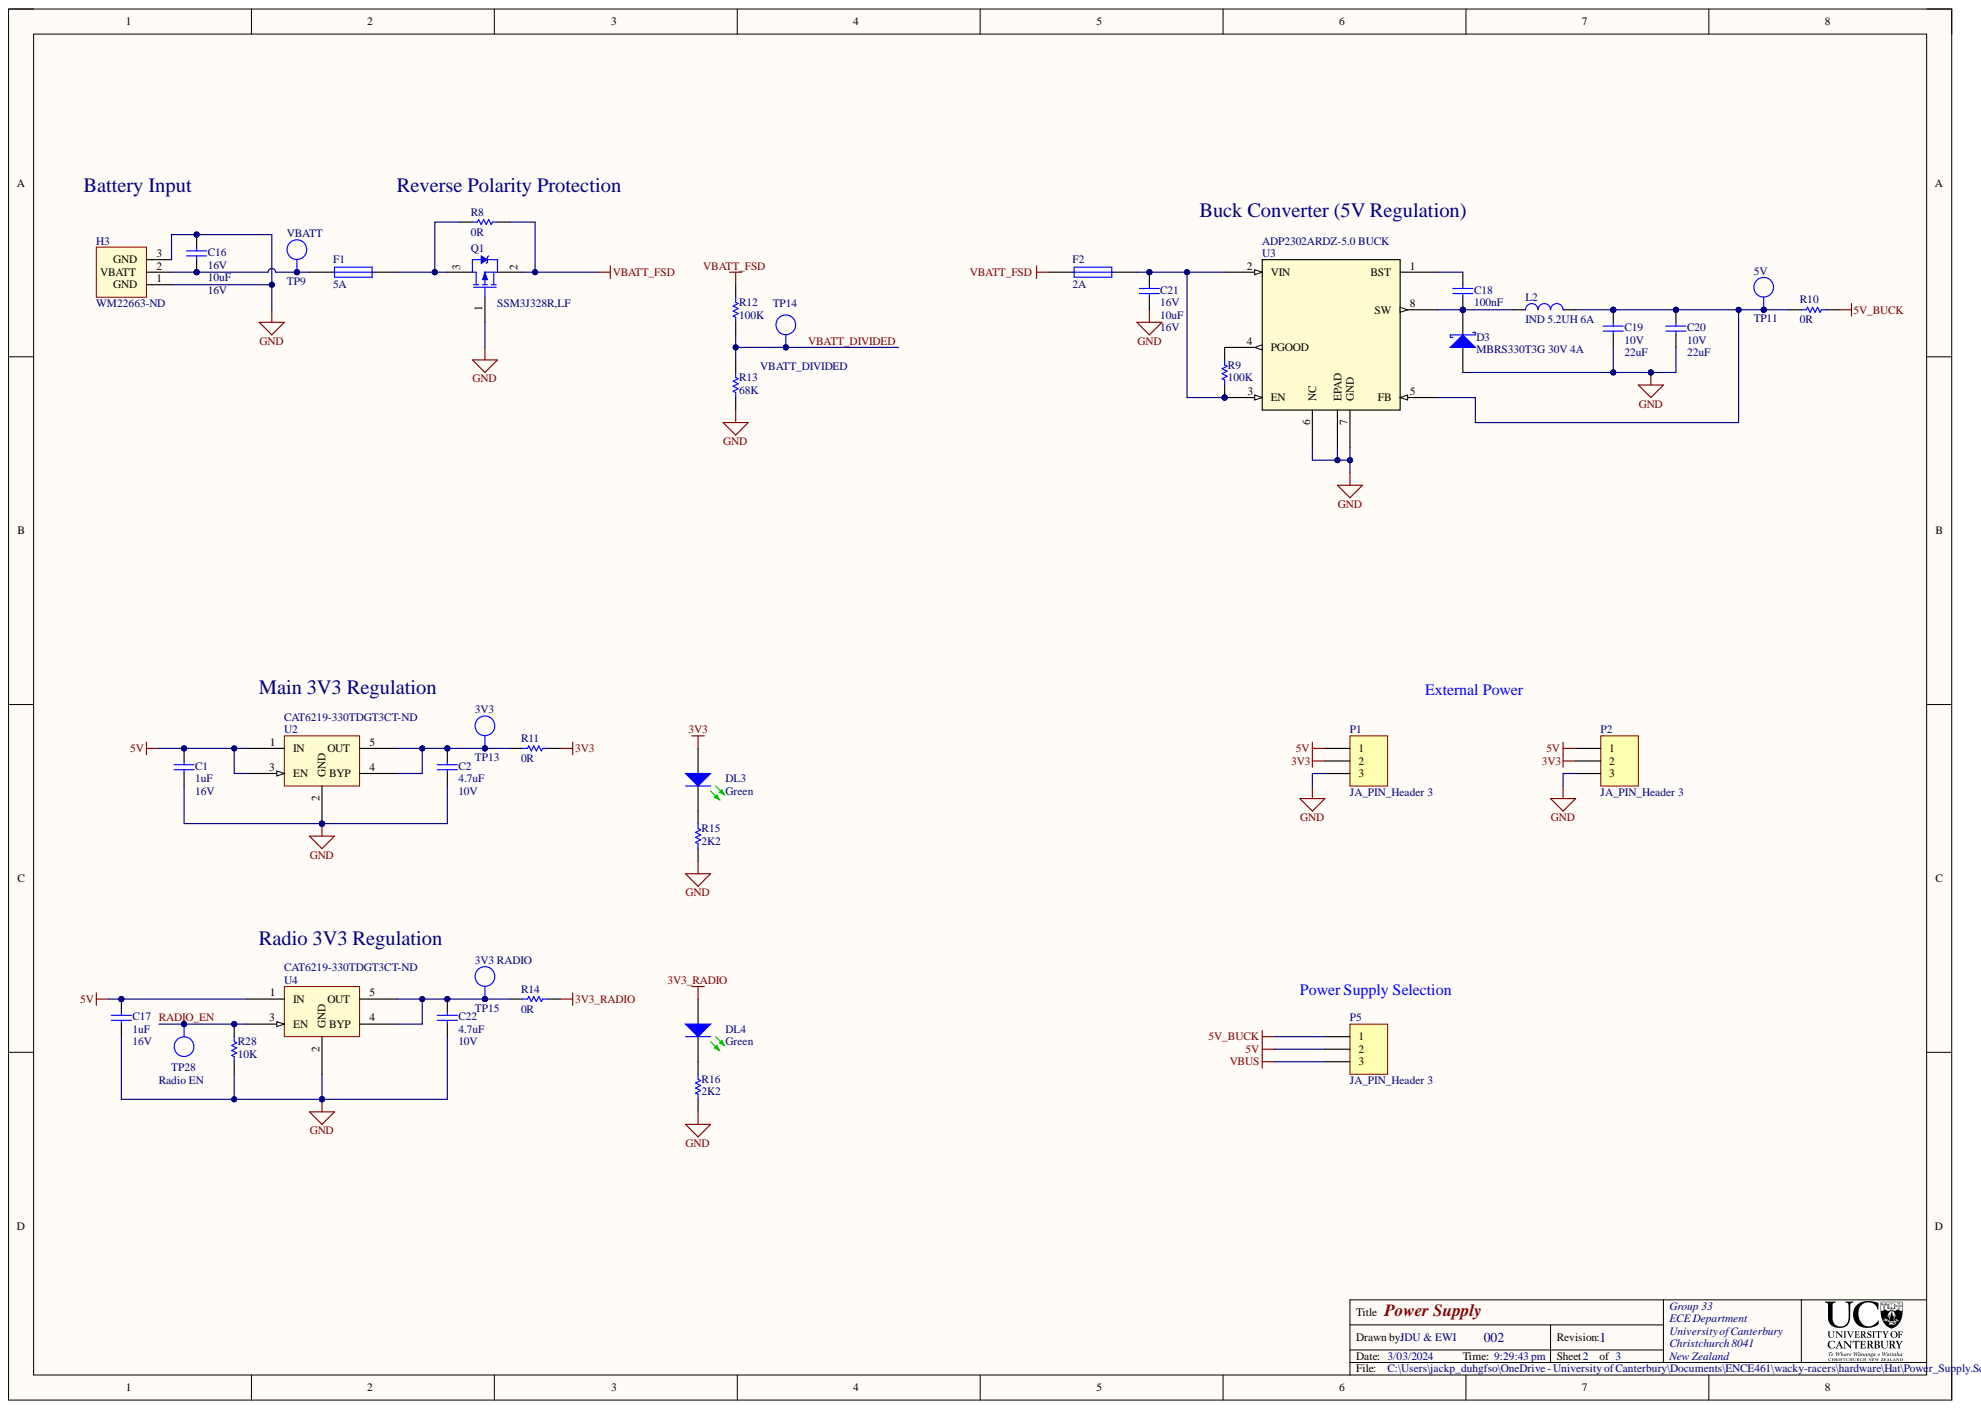
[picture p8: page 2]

C:\Users\jackp_duhgfso\OneDrive - University ofCanterbury\Documents\ENCE461\wacky-racers\hardware\Hat\Power_Supply.SchDoc

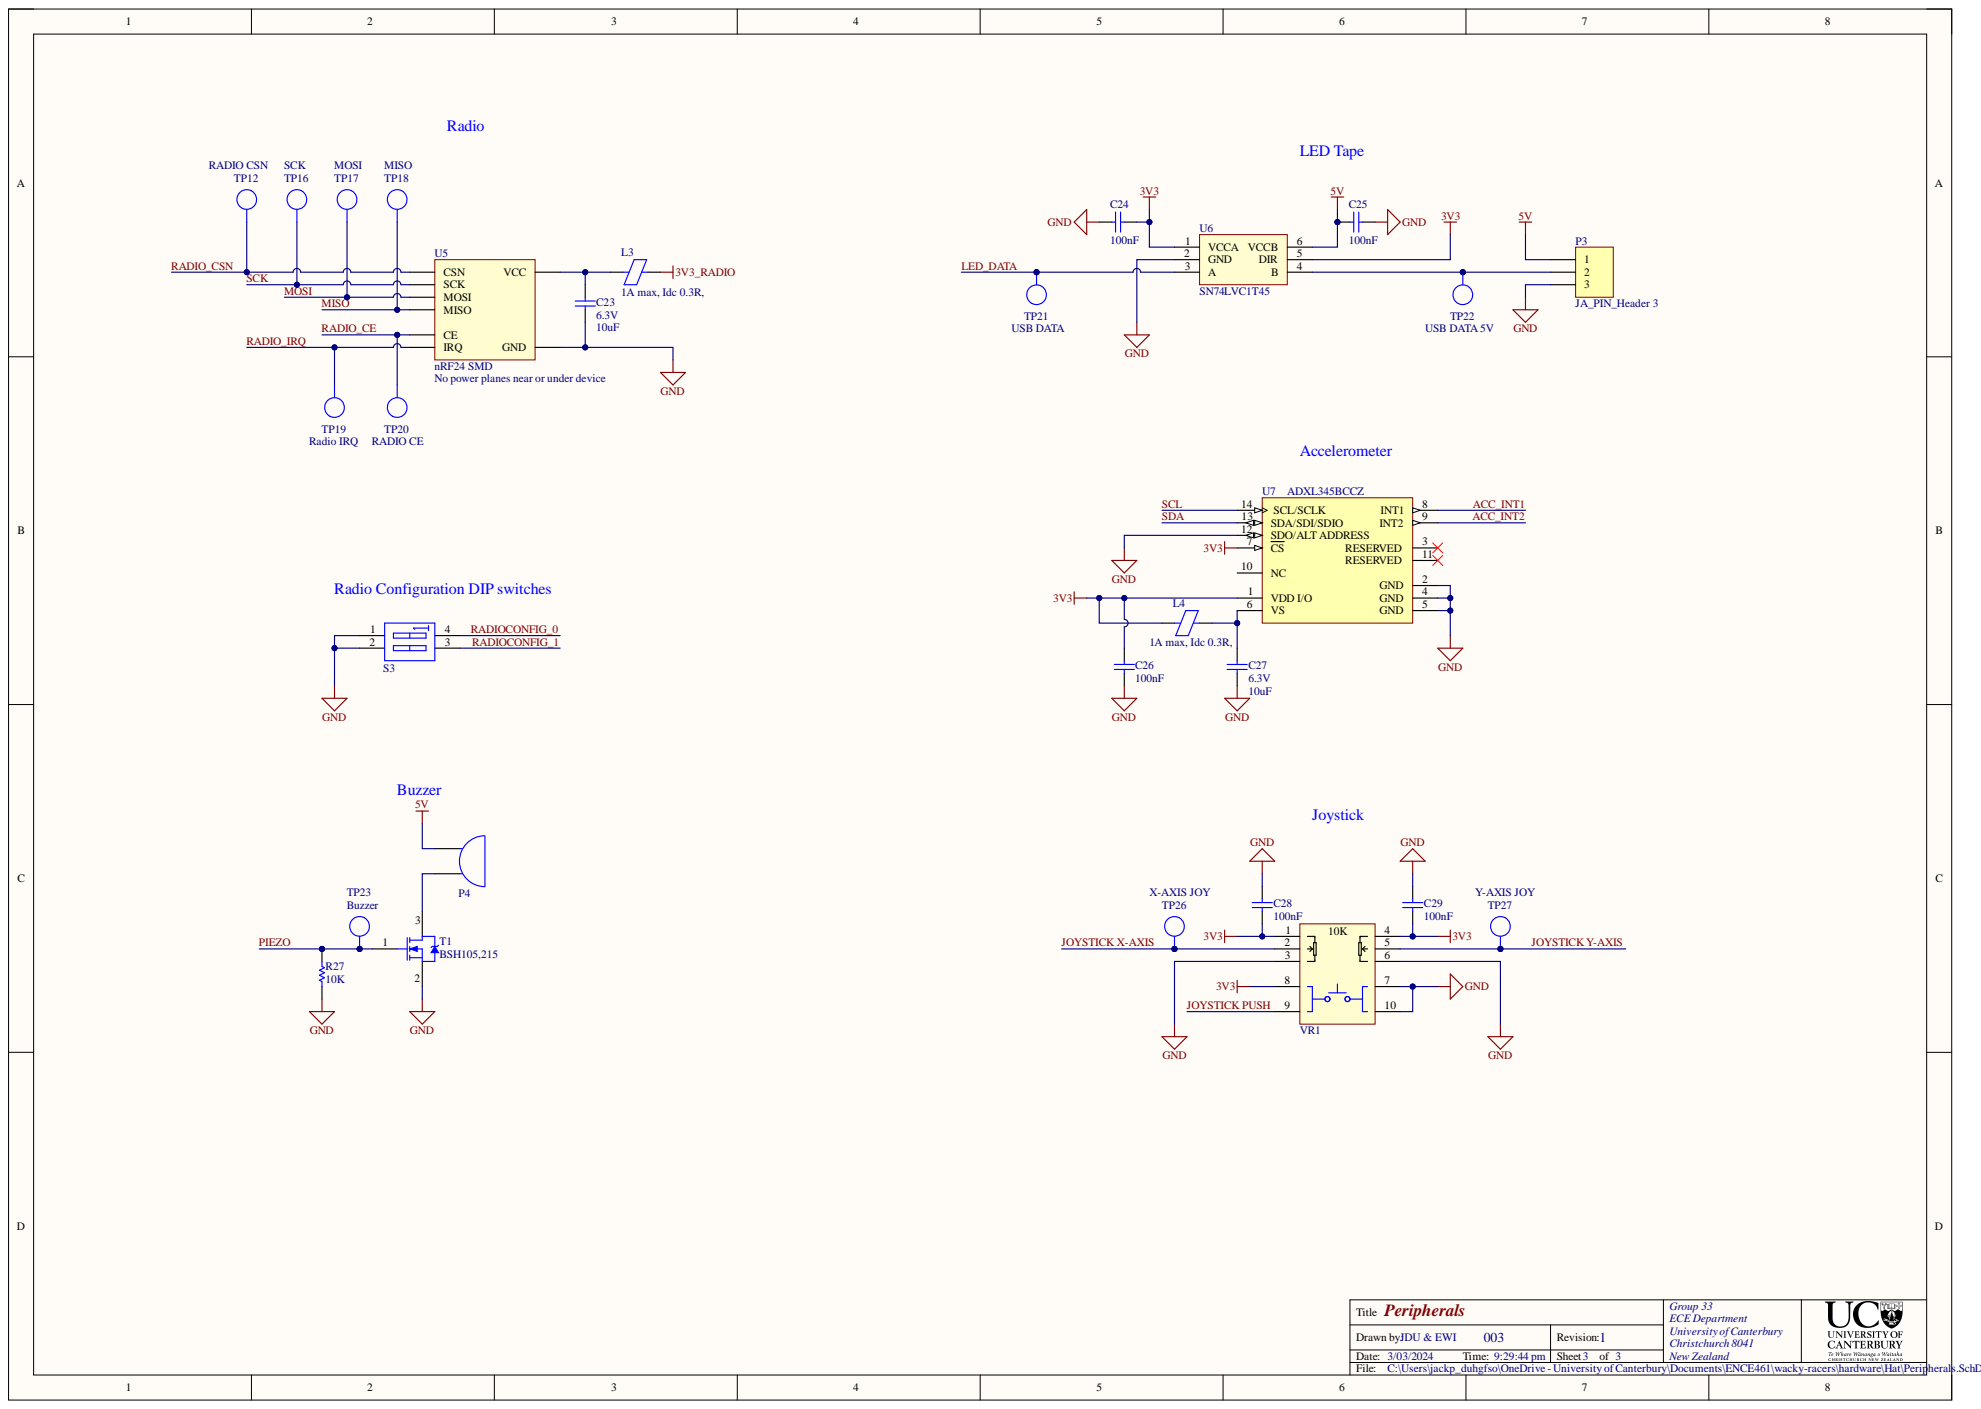
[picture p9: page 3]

IRQ
nRF24 SMD
No power planes near or under device

Radio Configuration DIP switches

C:\Users\jackp_duhgfso\OneDrive - University ofCanterbury\Documents\ENCE461\wacky-racers\hardware\Hat\Peripherals.SchDoc

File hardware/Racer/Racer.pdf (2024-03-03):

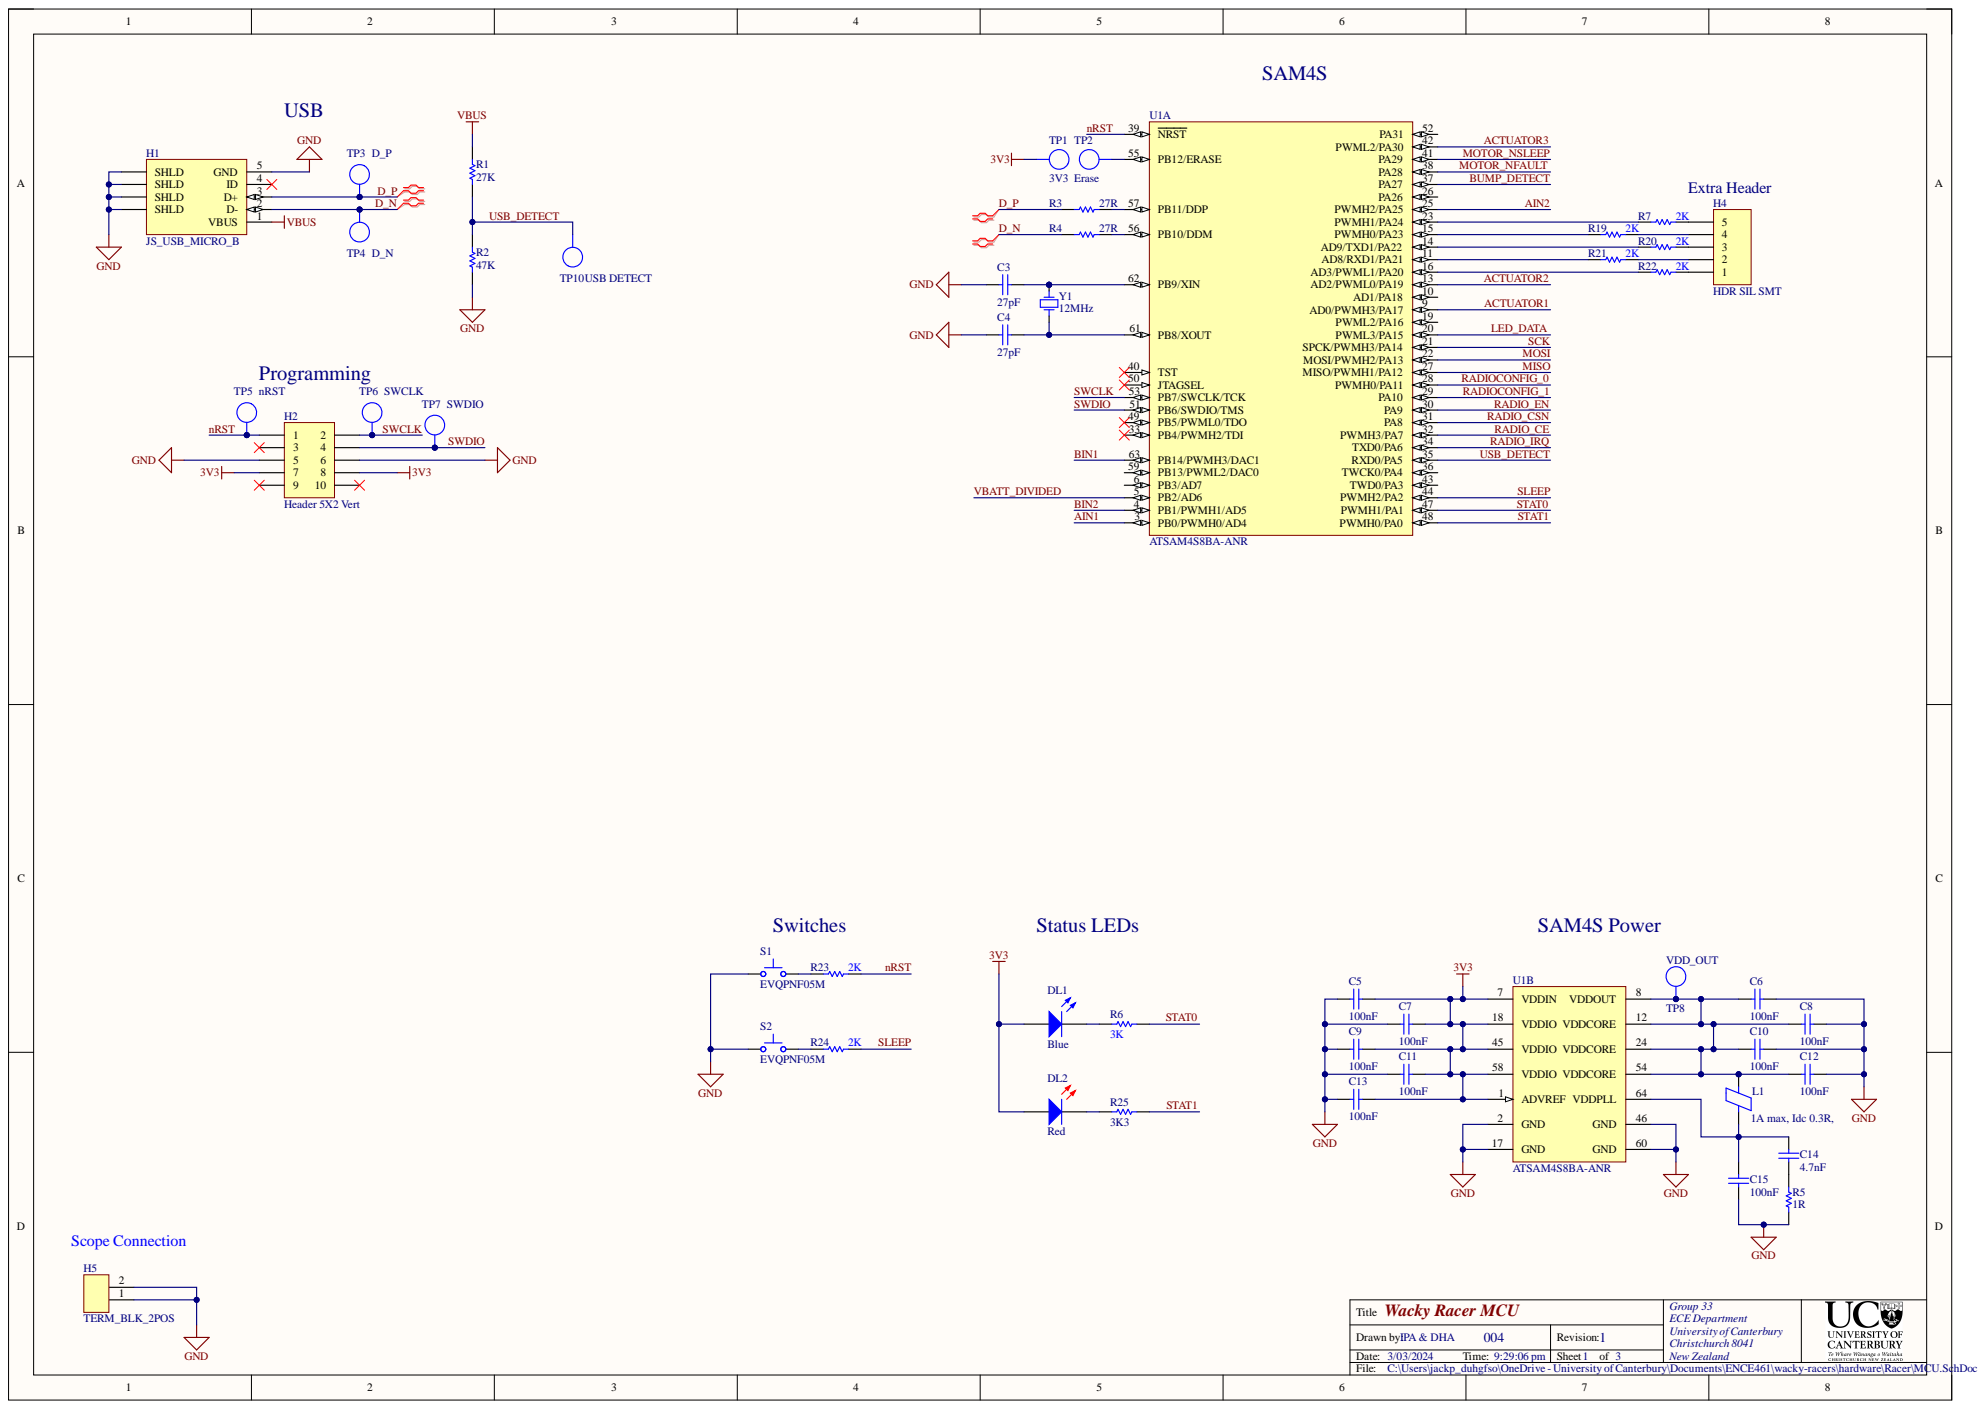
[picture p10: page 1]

Drawn by:
C:\Users\jackp_duhgfso\OneDrive - University ofCanterbury\Documents\ENCE461\wacky-racers\hardware\Racer\MCU.SchDoc

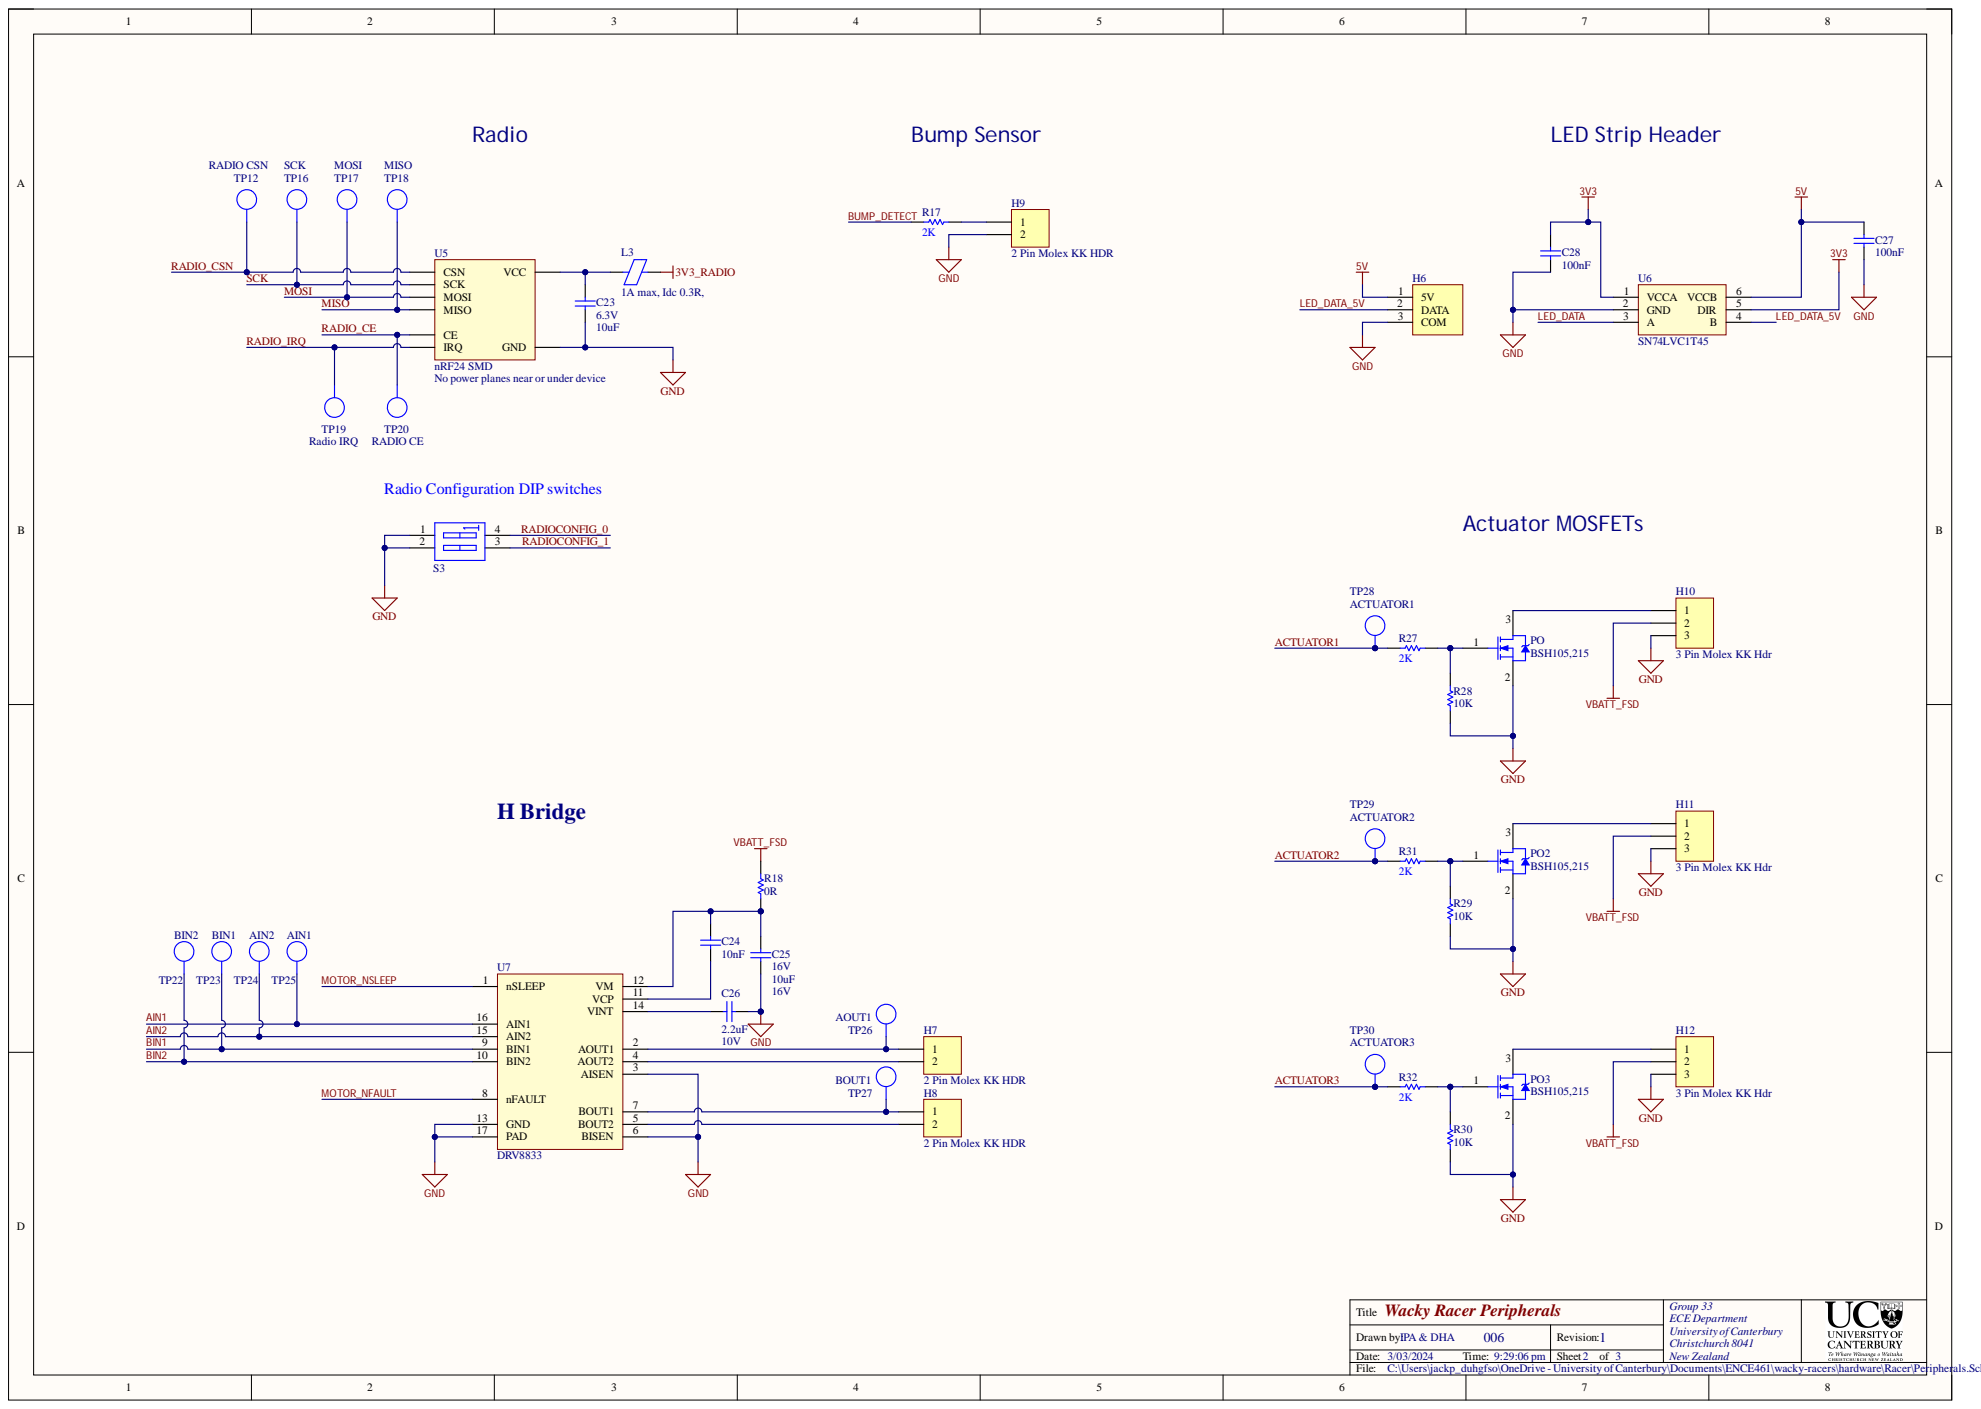
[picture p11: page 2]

IRQ
nRF24 SMD
No power planes near or under device

Radio Configuration DIP switches

C:\Users\jackp_duhgfso\OneDrive - University ofCanterbury\Documents\ENCE461\wacky-racers\hardware\Racer\Peripherals.SchDoc

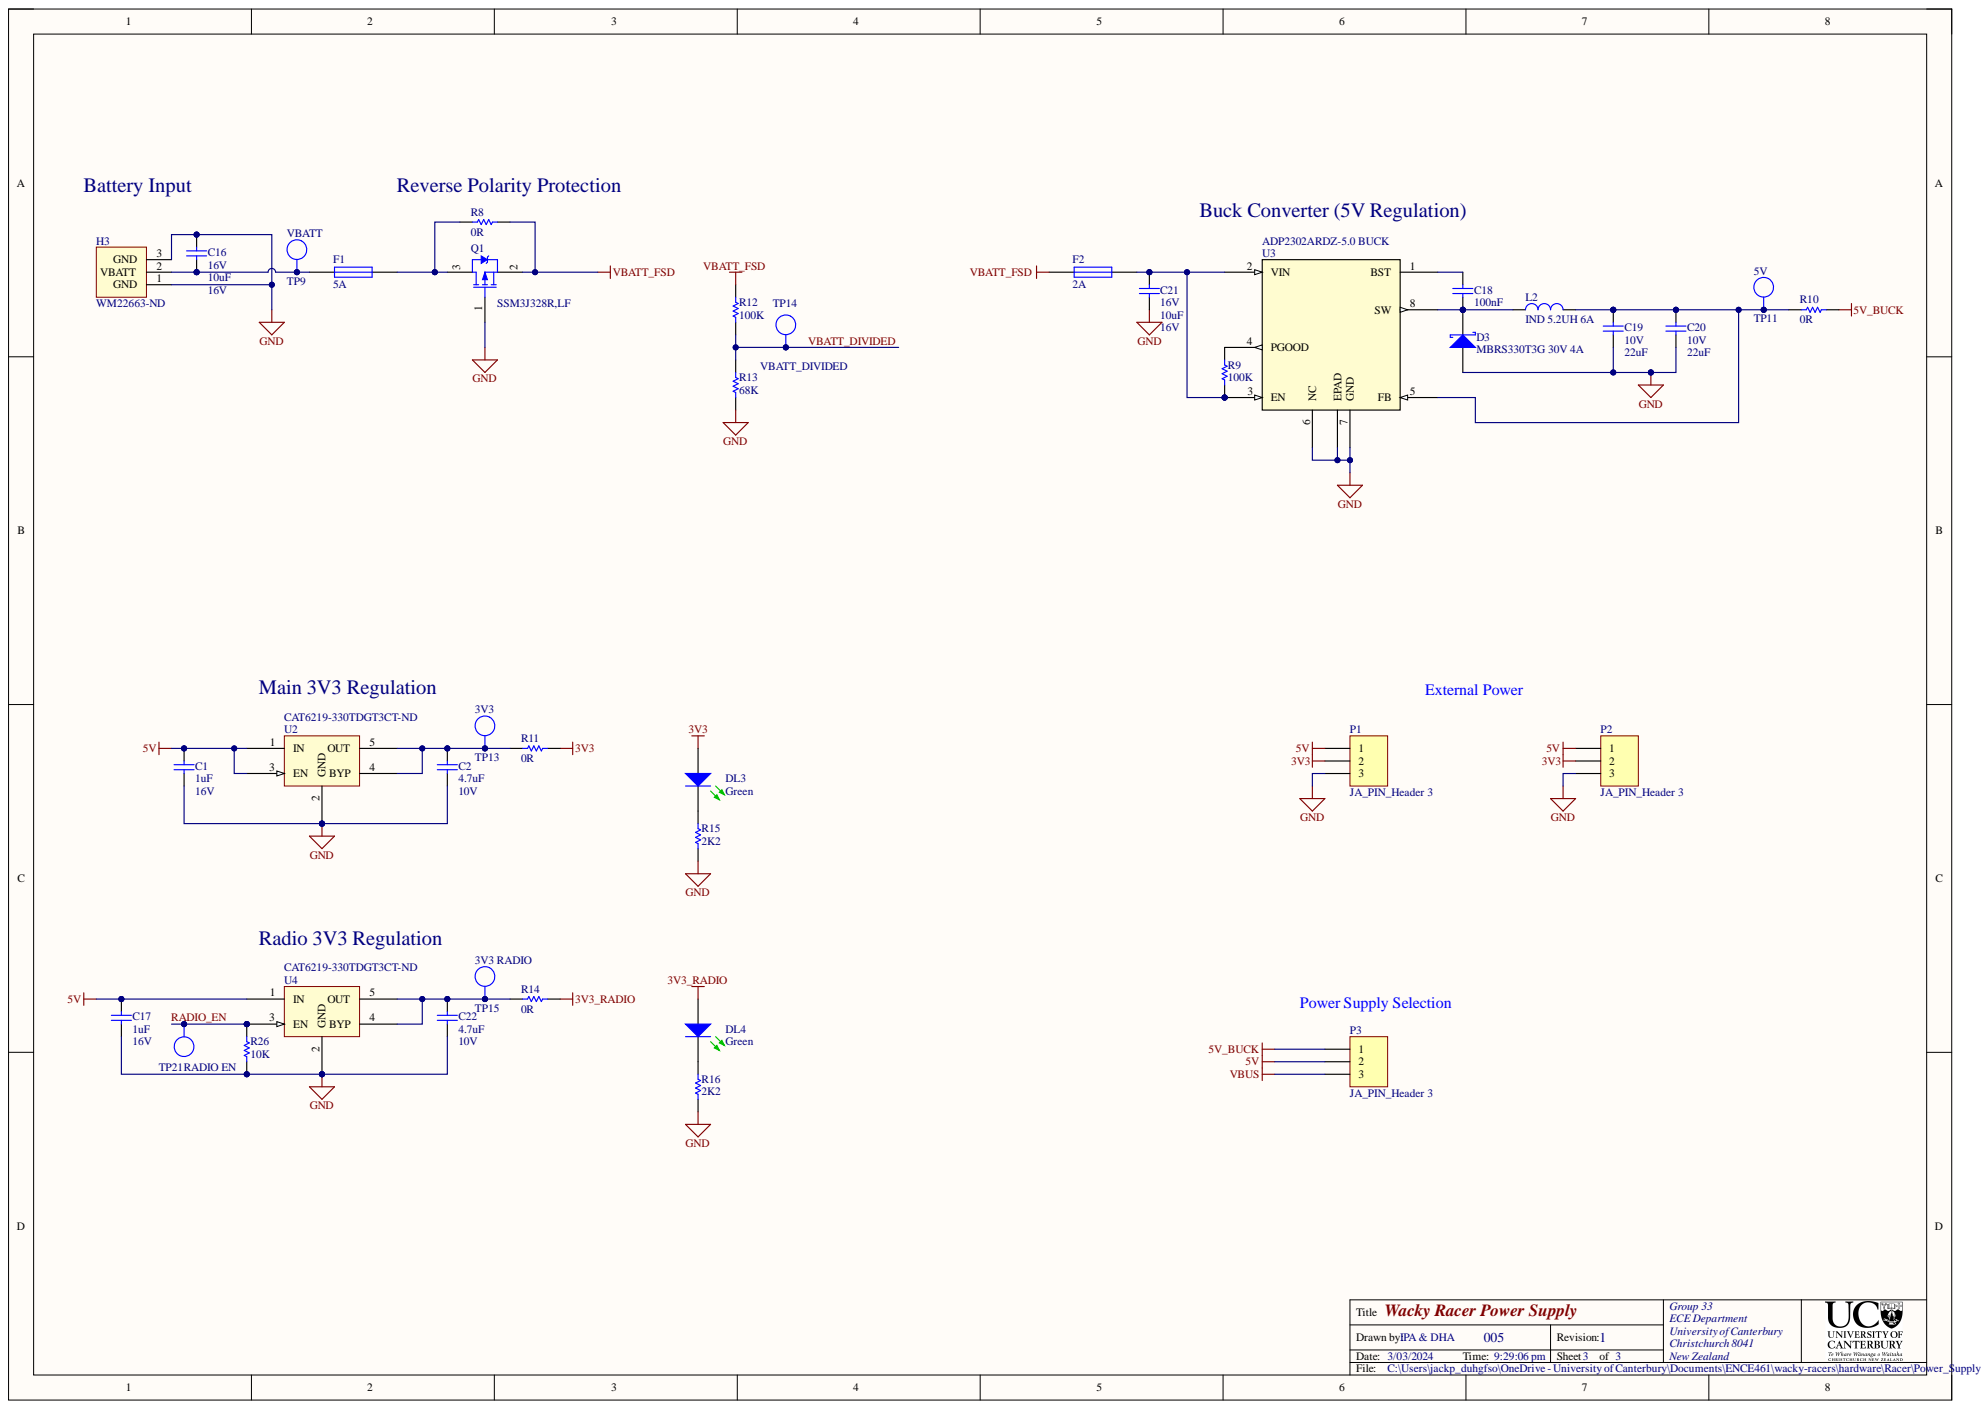
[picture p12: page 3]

Wacky Racer Power Supply

C:\Users\jackp_duhgfso\OneDrive - University ofCanterbury\Documents\ENCE461\wacky-racers\hardware\Racer\Power_Supply.SchDoc

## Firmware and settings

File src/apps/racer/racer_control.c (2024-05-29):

/* File:   radio_drive.c
   Author: I Patel & D Hawes
   Date:   9 May 2024
   Descr:  combines hbridge file and calls radio functions 
*/
#include <stdint.h>
#include <stdbool.h>

#include <pio.h>
#include "usb_serial.h" 
#include "pwm.h"
#include "delay.h"
#include "panic.h"
#include "pacer.h"
#include "led_tape.h"
#include "battery.h"
#include "mcu_sleep.h"

#include "radio.h"
#include "motor_control.h"

#include "target.h"

#define DELAY_MS 10

#define PACER_RATE 100
#define RX_RATE 50
#define TX_RATE 10
#define BATTERY_RATE 1
#define SLEEP_CHECK_RATE 1

#define RAMP_STEP 1
#define RAMP_DELAY 10

bool button_press = false;

// void ramp_duty_cycle(int *current_left_duty, int target_left_duty, int *current_right_duty, int target_right_duty) {
//     while (*current_left_duty != target_left_duty || *current_right_duty != target_right_duty) {
//         printf("RAMP\n");
//         // printf("Left Motor: %d, Right Motor: %d", current_left_duty, current_right_duty);
//         if (*current_left_duty < target_left_duty) {
//             *current_left_duty += RAMP_STEP;
//             if (*current_left_duty > target_left_duty) {
//                 *current_left_duty = target_left_duty;
//             }
//         } else if (*current_left_duty > target_left_duty) {
//             *current_left_duty -= RAMP_STEP;
//             if (*current_left_duty < target_left_duty) {
//                 *current_left_duty = target_left_duty;
//             }
//         }

//         if (*current_right_duty < target_right_duty) {
//             *current_right_duty += RAMP_STEP;
//             if (*current_right_duty > target_right_duty) {
//                 *current_right_duty = target_right_duty;
//             }
//         } else if (*current_right_duty > target_right_duty) {
//             *current_right_duty -= RAMP_STEP;
//             if (*current_right_duty < target_right_duty) {
//                 *current_right_duty = target_right_duty;
//             }
//         }

//         set_duty(*current_left_duty, *current_right_duty); // Update both motors
//         delay_ms(RAMP_DELAY);
//     }
//     printf("Ramp done\n");
// }

// void ramp_duty_cycle(int *current_left_duty, int target_left_duty, int *current_right_duty, int target_right_duty) 
// {
//     printf("MOTOR SET %d, %d\n", target_left_duty, target_right_duty);
//     set_duty(target_left_duty, target_right_duty);
// }



/***
 * adapts h bridge main to include init radio and ready to recieve radio
 * unsure if radio_rx needs to be in the while loop or seperate
 * will also write the values to the serial to allow for debugging
 * radio_tx is written, but will need to be triggered by the bumper
 * * the bumper acts as a switch to move the radio from rx to tx
 * * could set up bumper as an interrupt??
 * if it shits itself, could be bc of attempting serial and radio???
 ***/

void sleepify(void) {
    mcu_sleep_cfg_t sleep_cfg = {.mode=MCU_SLEEP_MODE_BACKUP};
    mcu_sleep_wakeup_cfg_t sleep_wakeup_cfg = {
        .pio = BUTTON_PIO,
        .active_high = false,
    };

    led_tape_off();
    radio_power_down();
    // motor_power_down();
    pio_output_high(LED_STATUS_PIO);
    pio_output_high(LED_ERROR_PIO);

    delay_ms(3000);

    mcu_sleep_wakeup_set(&sleep_wakeup_cfg);
    mcu_sleep(&sleep_cfg);
}


int main (void)
{
    // init pwm //
    motor_init();
    led_tape_driving();
    
    battery_sensor_init();

    bool asked = false;

    // pio_config_set (LED_STATUS_PIO, PIO_OUTPUT_HIGH);    

    int i = 0;
    if(usb_serial_stdio_init() < 0) 
        panic(LED_ERROR_PIO, 3);

    // pio_config_set (LED_STATUS_PIO, PIO_OUTPUT_HIGH);
    
    pacer_init(PACER_RATE);

    // all new below //

    radio_init();   // init radio
    pio_config_set(BUMP_DETECT, PIO_INPUT); // sets bumper pin as input
    pio_config_set(BUMP_DETECT, PIO_PULLUP);

    pio_config_set (LED_STATUS_PIO, PIO_OUTPUT_HIGH);
    pio_config_set (LED_ERROR_PIO, PIO_OUTPUT_LOW);

    // creates variables for setting duty
    int prev_left_duty = 0;
    int prev_right_duty = 0;
    int left_motor_duty = 0;
    int right_motor_duty = 0;
    int dastardly;
    int parity;
    uint8_t hit_signal;
    uint32_t tick_tx = 0;
    uint32_t tick_rx = 0;
    uint32_t tick_battery = 0;
    uint32_t tick_sleep = 0;
    char radio_message[33];
    bool listening = true;
    bool hit_detect = true;
    bool hit_detect_flag = true;

    while (1)
    {   
        pacer_wait();
        tick_rx++;
        tick_tx++;
        tick_battery++;
        tick_sleep++;

        // set_duty(0, 0);
        hit_detect = pio_input_get(BUMP_DETECT);
        if (!hit_detect) hit_detect_flag = false;

        if(tick_tx > (PACER_RATE/TX_RATE)) {
            // pio_output_set(TX_LED, 0); // tells its in tranmitting mode
            // pio_output_set (RX_LED, 1);
            int tx_status;
            tx_status = radio_tx(hit_detect_flag);
            // pio_output_set(TX_LED, 1);

            if (tx_status == 32) {
                hit_detect_flag = true;
            }
            
            radio_listen();
            tick_tx = 0;
        } 

        if (tick_rx > (PACER_RATE/RX_RATE)) {
            if (radio_rx_data_ready()) {
                // pio_output_set (RX_LED, 0);
                // pio_output_set(TX_LED, 1);

                char buffer[32] = {0};

                radio_rx(buffer);

                printf("%s\n", buffer);
                printf("TX\n");

                sscanf(buffer, "%d,%d,%d,%d", &left_motor_duty, 
                &right_motor_duty,&dastardly,&parity);

                printf("Set: %3d,%3d,%2d,%1d\n", left_motor_duty, right_motor_duty, dastardly, parity);

                if (left_motor_duty >= 80) {
                    left_motor_duty = 80;
                } else if (left_motor_duty <= -80) {
                    left_motor_duty = -80;
                }
                if (right_motor_duty >= 80) {
                    right_motor_duty = 80;
                } else if (right_motor_duty <= -80) {
                    right_motor_duty = -80;
                }

                if (left_motor_duty<=5 && left_motor_duty>=-5) {
                    left_motor_duty = 0;
                } else if (right_motor_duty<=5 && right_motor_duty>=-5) {
                    right_motor_duty = 0;
                }

                if (dastardly == 1) {
                    led_tape_bump();
                } else {
                    led_tape_driving();
                }
                // ramp_duty_cycle(&prev_left_duty, left_motor_duty, &prev_right_duty, right_motor_duty);
                // prev_right_duty=right_motor_duty;
                // prev_left_duty=left_motor_duty;
                set_duty(left_motor_duty, right_motor_duty);

            }
            tick_rx = 0;
            // printf ("listening\n");
        }
        
        //Check Battery Value
        if (tick_battery>(PACER_RATE/BATTERY_RATE)) {
            if (battery_millivolts() < 2453)
            {
                pio_output_toggle(LED_ERROR_PIO);
                pio_output_high(LED_STATUS_PIO);
                delay_ms(10);
            }  else {
                pio_output_toggle(LED_STATUS_PIO);
                pio_output_high(LED_ERROR_PIO);
            }
            tick_battery=0;
        }

        if (tick_sleep > (PACER_RATE/SLEEP_CHECK_RATE)) {
            if (pio_input_get(BUTTON_PIO) == 0) {
                sleepify();
            }
            tick_sleep = 0;
        }
        
    }
}

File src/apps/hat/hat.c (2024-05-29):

/** 
 * @file hat.c
 * @author Jack Duignan (Jdu80@uclive.ac.nz)
 * @date 2024-04-22
 * @brief This is the main file for the hat program
 */

/**
 * Overview:
 * 
 * This program does 3 things:
 * Transmits the accelerometer readings as duty cycles at a rate of 
 * RADIO_SEND_RATE unless the bumper is hit when it send 0s
 * If the bumper is hit it activates the led strip
 * 
 * It plays a song on the buzzer
 * 
 * Receives only when data is available at a rate of RADIO_RX_RATE there is 
 * no waiting after a successful rx so care should be taken to ensure that tx 
 * from the other device is not to large.
*/


#include <stdint.h>
#include <stdbool.h>
#include <stdio.h>

#include <pio.h>

#include "pacer.h"
#include "usb_serial.h"
#include "panic.h"
#include "delay.h"

#include "control.h"
#include "communications.h"
#include "target.h"
#include "buzzer.h"
#include "led_tape.h"
#include "battery.h"
#include "mcu_sleep.h"

// Game constants
#define STOP_TIME 5 //< The stop time in seconds
#define BATTERY_DROP_LIMIT 0 //< The number of times a battery drop is detected

// Pacer Constants in Hz
#define PACER_RATE 100
#define CONTROL_UPDATE_RATE 5
#define RADIO_SEND_RATE 30
#define RADIO_RECEIVE_RATE 50
#define BUZZER_UPDATE_RATE 4
#define LED_UPDATE_RATE 2
#define BATTERY_CHECK_RATE 1
#define SLEEP_CHECK_RATE 2

// Enables
bool g_radio_en = true;
bool g_control_en = true;
bool g_buzzer_en = true;
bool g_led_en = true;
bool g_battery_check_en = true;
bool g_sleep_en = true;

control_data_t g_control_data; 
radio_packet_t g_radio_packet;

// Bumper control
bool g_bumper_hit = false;
bool g_stopped = false;

/** 
 * @brief Handle the radio tx functionality
 * 
 */
void radio_tx_handler(void) {
    int8_t get_result;
    if ((get_result = control_get_data(&g_control_data)) != 0) {
        printf ("Acc Error\n");
    }

    if (g_stopped) {
        g_control_data.left_motor = 0;
        g_control_data.right_motor = 0;
    }

    g_radio_packet.left_duty = g_control_data.left_motor;
    g_radio_packet.right_duty = g_control_data.right_motor;
    g_radio_packet.dastardly = g_stopped;
    g_radio_packet.parity = 1;

    if (radio_tx(&g_radio_packet, false)) {
        // printf ("Tx Error\n");
    }
}


void setup (void) {
    usb_serial_stdio_init ();

    pio_config_set(LED_STATUS_PIO, PIO_OUTPUT_HIGH);
    pio_config_set(LED_ERROR_PIO, PIO_OUTPUT_HIGH);
    pio_config_set(RADIO_POWER_ENABLE_PIO, PIO_OUTPUT_HIGH);

    pio_output_set(LED_STATUS_PIO, LED_ACTIVE);
    
    pio_config_set(BUTTON_PIO, PIO_PULLUP);

    if (radio_init()) {
        panic (LED_ERROR_PIO, 4);
    }

    if (!g_radio_en) {
        radio_power_down();
    }

    if (control_init(ADXL345_ADDRESS, false)) {
        panic (LED_ERROR_PIO, 12);
    }

    if (buzzer_init()) {
        panic (LED_ERROR_PIO, 6);
    }

    if (!g_buzzer_en) {
       buzzer_off();
    } 

    if (led_tape_init()) {
        panic (LED_ERROR_PIO, 8);
    }

    if (!g_led_en) {
        led_tape_off();
    }

    if (battery_sensor_init()) {
        panic (LED_ERROR_PIO, 10);
    }
}


void sleepify(void) {
    mcu_sleep_cfg_t sleep_cfg = {.mode=MCU_SLEEP_MODE_BACKUP};
    mcu_sleep_wakeup_cfg_t sleep_wakeup_cfg = {
        .pio = BUTTON_PIO,
        .active_high = false,
    };

    led_tape_off();
    radio_power_down();
    buzzer_off();
    pio_output_high(LED_STATUS_PIO);
    pio_output_high(LED_ERROR_PIO);

    delay_ms(3000);

    mcu_sleep_wakeup_set(&sleep_wakeup_cfg);
    mcu_sleep(&sleep_cfg);
}


int main (void) {
    uint32_t ticks_control = 0;
    uint32_t ticks_tx = 0;
    uint32_t ticks_rx = 0;
    uint32_t ticks_buzzer = 0;
    uint32_t ticks_led = 0;
    uint32_t ticks_battery = 0;
    uint32_t ticks_sleep = 0;

    uint32_t ticks_stopped = 0;

    uint32_t battery_drop_num = 0;

    setup();

    pacer_init(PACER_RATE);

    while (1) {
        pacer_wait();
        ticks_control++;
        ticks_rx++;
        ticks_tx++;
        ticks_buzzer++;
        ticks_led++;
        ticks_stopped++;
        ticks_battery++;
        ticks_sleep++;

        // Stopped from bumper control
        if (g_bumper_hit && !g_stopped 
            && (ticks_stopped > (STOP_TIME+2) * PACER_RATE)) 
        {
            g_stopped = true;
            ticks_stopped = 0;
            g_bumper_hit = false;
        } else if (g_stopped && (ticks_stopped > STOP_TIME*PACER_RATE)) {
            g_stopped = false;
        } else if (ticks_stopped > (UINT32_MAX - 100)) { // Control over flow
            ticks_stopped = 0;
        }

    	// Control Update
        if (g_control_en && (ticks_control > (PACER_RATE / CONTROL_UPDATE_RATE))) {
            control_update();
            ticks_control = 0;
        } 

        // Radio tx
        if (g_radio_en && (ticks_tx > (PACER_RATE / RADIO_SEND_RATE))) {
            radio_tx_handler();

            radio_listen(); // Set back to read mode
            ticks_tx = 0;
        }

        // Radio Rx
        if (g_radio_en && (ticks_rx > (PACER_RATE / RADIO_RECEIVE_RATE))) {
            if (radio_rx_data_ready()) { // only read if you have too
                int8_t result = radio_get_bumper();

                if (result != -1) {
                    printf("                             Rx: %d\n", result);   
                } 
                
                if (result == 0 && !g_stopped) {
                    g_bumper_hit = true;
                } else {
                    g_bumper_hit = false;
                }
            }

            ticks_rx = 0;
        } 

        // Buzzer sound update
        if (g_buzzer_en && (ticks_buzzer > (PACER_RATE / BUZZER_UPDATE_RATE))) {
            buzzer_update(g_stopped);
            ticks_buzzer = 0;
        }

        // Led strip update
        if (g_led_en && (ticks_led > (PACER_RATE / LED_UPDATE_RATE))) {
            led_tape_update(g_stopped);
            ticks_led = 0;
        }   

        // Battery voltage switch
        if (g_battery_check_en 
            && (ticks_battery > (PACER_RATE / BATTERY_CHECK_RATE))) {
            if (battery_millivolts() < 2553) {
                battery_drop_num++;
            } else {
                battery_drop_num = 0;
                pio_output_high(LED_ERROR_PIO);
            }

            if (battery_drop_num > BATTERY_DROP_LIMIT) {
                // radio_power_down();
                // led_tape_off();
                // buzzer_off();
                // pio_output_high(LED_STATUS_PIO);
                pio_output_toggle(LED_ERROR_PIO);   
            }

            ticks_battery = 0;
        }

        // Sleep checking
        if (g_sleep_en && ticks_sleep > (PACER_RATE/SLEEP_CHECK_RATE)) {
            
            if (pio_input_get(BUTTON_PIO) == 0) {
                sleepify();
            }
            ticks_sleep = 0;
        }
    }
}

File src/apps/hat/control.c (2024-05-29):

/** 
 * @file CTR_control.c
 * @author Jack Duignan (Jdu80@uclive.ac.nz)
 * @date 2024-04-25
 * @brief Accelerometer processing implementation
 * 
 * This file implements both accelerometer proccessing and converting the 
 * raw data to control inputs to be sent over radio.
 *
 * Accelerometer Settings:
 * FIFO_CTL 0x80 - stream mode FIFO holds last 32 values and overwrites
 * POWER_CTL 0x08 - measure bit
 * DATA_FORMAT 0x08 - Full resolution mode +-2g (4mg/LSB scale)
 */


#include <stdint.h>
#include <stdbool.h>
#include <stdio.h>


#include "adxl345.h"

#include "circular_buffer.h"

#include "control.h"

#define BUFFER_SIZE 8

/// The steering angles divisor to go from accelerometer value to duty cycle
#define STEERING_DIVISOR 7 // value*2/divisor
#define STEERING_MAX 60
#define STEERING_MIN -60

/// The throttle divisor to go from accelerometer value to duty cycle
#define THROTTLE_DIVISOR 4 // value*2/divisor
#define THROTTLE_MAX 80
#define THROTTLE_MIN -80

/// The maximums for duty cycle for the left and right motor
#define LEFT_MOTOR_MAX 80
#define LEFT_MOTOR_MIN -80

#define RIGHT_MOTOR_MAX 80
#define RIGHT_MOTOR_MIN -80


static twi_t adxl345_twi;
static adxl345_t *adxl345;

circ_buff_t x_buffer, y_buffer, z_buffer;

static twi_cfg_t adxl345_twi_cfg =
{
    .channel = TWI_CHANNEL_0,
    .period = TWI_PERIOD_DIVISOR (100000), // 100 kHz
    .slave_addr = 0
};

bool g_buff_en = false;

int8_t control_init (twi_slave_addr_t slave_addr, bool buff_en) {
    adxl345_twi = twi_init(&adxl345_twi_cfg);

    if (!adxl345_twi) return 1; // twi failed

    adxl345 = adxl345_init (adxl345_twi, slave_addr);

    if (!adxl345) return 2; // adx failed

    if (buff_en) {
        g_buff_en = true;

        circ_buff_init(&x_buffer, BUFFER_SIZE);
        circ_buff_init(&y_buffer, BUFFER_SIZE);
        circ_buff_init(&z_buffer, BUFFER_SIZE);
    }

    return 0;
}


static int8_t get_raw_data (int16_t accel[3]) {
    if (! adxl345_is_ready (adxl345)) return 1; // Not ready
    
    if (adxl345_accel_read (adxl345, accel)) return 0; // Complete
    else return 2; // Read Failed
}


int8_t control_update (void) {
    if (!g_buff_en) return 3;

    int16_t accel[3];
    
    int8_t r_readResult = get_raw_data(accel);

    if (r_readResult == 0) {
        circ_buff_write(&x_buffer, (int32_t)accel[0]);
        circ_buff_write(&y_buffer, (int32_t)accel[1]);
        circ_buff_write(&z_buffer, (int32_t)accel[2]);
    }

    return r_readResult;
}


/** 
 * @brief Calculate the steering angle for the car
 * @param raw_x the raw accelerometer value
 * 
 * @return the duty cycle from -100 to 100
 */
static int8_t calc_steering(int16_t raw_x) {
    int16_t r_control_value =  raw_x*2 / STEERING_DIVISOR;

    if (r_control_value >= 0 && r_control_value > STEERING_MAX) {
        r_control_value = STEERING_MAX;
    } else if (r_control_value < 0 && r_control_value < STEERING_MIN) {
        r_control_value = STEERING_MIN;
    }

    return (int8_t)r_control_value;
}

/** 
 * @brief Calculate the throotle level for the var
 * @param raw_y the raw accelerometer value
 * 
 * @return the duty cycle from THROTTLE_MAX to THROTTLE_MIN
 */
static int8_t calc_throttle(int16_t raw_y) {
    int16_t r_control_value =  raw_y*2 / THROTTLE_DIVISOR;

    if (r_control_value >= 0 && r_control_value > THROTTLE_MAX) {
        r_control_value = THROTTLE_MAX;
    } else if (r_control_value < 0 && r_control_value < THROTTLE_MIN) {
        r_control_value = THROTTLE_MIN;
    }

    return (int8_t)r_control_value;
}


int8_t control_get_data (control_data_t *control_data) {
    int8_t r_read_result = 0;

    if (g_buff_en) { // Get buffer values
        control_data->raw_x = circ_buff_mean(&x_buffer);
        control_data->raw_y = circ_buff_mean(&y_buffer);
        control_data->raw_z = circ_buff_mean(&z_buffer);

    } else { // Get the raw values (slower for update but don't need control 
             // update function)
        int16_t accel[3];
    
        r_read_result = get_raw_data (accel);

        if (r_read_result == 0) {
            control_data->raw_x = accel[0];
            control_data->raw_y = accel[1];
            control_data->raw_z = accel[2];
        }
    }


    // Calculate the tank tracks
    int16_t steering = calc_steering(control_data->raw_x);
    int16_t throttle = calc_throttle(control_data->raw_y);

    // Steering = steering * 1 at throttle = 100%
    // Steering = steering * 0.5 at throttle = 0%
    int16_t normilised_throttle = throttle;

    if (throttle < 0) {
        normilised_throttle *= -1;
    }

    normilised_throttle = normilised_throttle * 100 / THROTTLE_MAX;
    int16_t interperlation = 100 / 2 + normilised_throttle / 2;

    steering = steering * interperlation / 100;


    int16_t left_motor = throttle + steering;
    int16_t right_motor = throttle - steering;

    if (left_motor > LEFT_MOTOR_MAX) {
        left_motor = LEFT_MOTOR_MAX;
    } else if (left_motor < LEFT_MOTOR_MIN) {
        left_motor = LEFT_MOTOR_MIN;
    }

    if (right_motor > RIGHT_MOTOR_MAX) {
        right_motor = RIGHT_MOTOR_MAX;
    } else if (right_motor < RIGHT_MOTOR_MIN) {
        right_motor = RIGHT_MOTOR_MIN;
    }

    control_data->left_motor = (int8_t)left_motor;
    control_data->right_motor = (int8_t)right_motor;

    return r_read_result;
}

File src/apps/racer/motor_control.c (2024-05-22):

/* File:   motor_control.c
   Author: I Patel & D Hawes
   Date:   9 May 2024
   Descr:  modulisation of pwm control
*/

#include <stdint.h>
#include <stdbool.h>

#include <pio.h>
#include "usb_serial.h" 
#include "pwm.h"
#include "delay.h"
#include "panic.h"
#include "pacer.h"

#include "radio.h"
#include "motor_control.h"

#include "target.h"

#define PWM1_PIO PA25_PIO //AIN1
#define PWM2_PIO PB14_PIO //BIN1
#define PWM3_PIO PB1_PIO //AIN2
#define PWM4_PIO PB0_PIO //BIN2

#define PWM_FREQ_HZ 500
#define START_DUTY_CYCLE 0

#define N_FAULT PA28_PIO // nFault pin
#define N_SLEEP PA29_PIO // nSleep pin

uint32_t duty_cycle_right = 0;
uint32_t duty_cycle_left = 0;

int duty_cycle_right_forwards = 0;
int duty_cycle_right_backwards = 0;
int duty_cycle_left_forwards = 0;
int duty_cycle_left_backwards = 0;

pwm_t pwm1;
pwm_t pwm2;
pwm_t pwm3;
pwm_t pwm4;

static const pwm_cfg_t pwm1_cfg =
    {
        .pio = PWM1_PIO,
        .period = PWM_PERIOD_DIVISOR (PWM_FREQ_HZ),
        .duty = PWM_DUTY_DIVISOR (PWM_FREQ_HZ, START_DUTY_CYCLE),
        .align = PWM_ALIGN_LEFT,
        .polarity = PWM_POLARITY_HIGH,
        .stop_state = PIO_OUTPUT_LOW,
    };


static const pwm_cfg_t pwm2_cfg =
{
    .pio = PWM2_PIO,
    .period = PWM_PERIOD_DIVISOR (PWM_FREQ_HZ),
    .duty = PWM_DUTY_DIVISOR (PWM_FREQ_HZ, START_DUTY_CYCLE),
    .align = PWM_ALIGN_LEFT,
    .polarity = PWM_POLARITY_HIGH,
    .stop_state = PIO_OUTPUT_LOW,
};


static const pwm_cfg_t pwm3_cfg =
{
    .pio = PWM3_PIO,
    .period = PWM_PERIOD_DIVISOR (PWM_FREQ_HZ),
    .duty = PWM_DUTY_DIVISOR (PWM_FREQ_HZ, START_DUTY_CYCLE),
    .align = PWM_ALIGN_LEFT,
    .polarity = PWM_POLARITY_HIGH,
    .stop_state = PIO_OUTPUT_LOW,
};


static const pwm_cfg_t pwm4_cfg =
{
    .pio = PWM4_PIO,
    .period = PWM_PERIOD_DIVISOR (PWM_FREQ_HZ),
    .duty = PWM_DUTY_DIVISOR (PWM_FREQ_HZ, START_DUTY_CYCLE),
    .align = PWM_ALIGN_LEFT,
    .polarity = PWM_POLARITY_HIGH,
    .stop_state = PIO_OUTPUT_LOW,
};

void motor_init(void) 
{
    pio_config_set(N_FAULT, PIO_INPUT);
    pio_config_set(N_FAULT, PIO_OUTPUT_HIGH);
    pio_config_set(N_SLEEP, PIO_OUTPUT_HIGH);
    pio_output_high(N_SLEEP);

    pwm1 = pwm_init (&pwm1_cfg);
    if (! pwm1)
        panic (LED_ERROR_PIO, 1);

    pwm2 = pwm_init (&pwm2_cfg);
    if (! pwm2)
        panic (LED_ERROR_PIO, 1);

    pwm3 = pwm_init (&pwm3_cfg);
    if (! pwm3)
        panic (LED_ERROR_PIO, 1);

    pwm4 = pwm_init (&pwm4_cfg);
    if (! pwm4)
        panic (LED_ERROR_PIO, 1);

    pwm_start(pwm1);
    pwm_start(pwm2);
    pwm_start(pwm3);
    pwm_start(pwm4);

    //Set PWM to 0
    pwm_duty_set(pwm1, PWM_DUTY_DIVISOR(PWM_FREQ_HZ, 0));
    pwm_duty_set(pwm2, PWM_DUTY_DIVISOR(PWM_FREQ_HZ, 0));
    pwm_duty_set(pwm3, PWM_DUTY_DIVISOR(PWM_FREQ_HZ, 0));
    pwm_duty_set(pwm4, PWM_DUTY_DIVISOR(PWM_FREQ_HZ, 0));
}   

void motor_power_down(void) 
{
    pio_config_set(N_SLEEP, PIO_OUTPUT_LOW);
}

void set_duty(int duty_cycle_left,int duty_cycle_right) 
{
    int duty_cycle_right_forwards = 0;
    int duty_cycle_right_backwards = 0;
    int duty_cycle_left_forwards = 0;
    int duty_cycle_left_backwards = 0;

    if (duty_cycle_left>= 100) duty_cycle_left = 98;
    if (duty_cycle_right>= 100) duty_cycle_right = 98;
    if (duty_cycle_left<= -100) duty_cycle_left = -98;
    if (duty_cycle_right<= -100) duty_cycle_right = -98;

    if (duty_cycle_right > 0) {
        duty_cycle_right_forwards = duty_cycle_right;
        duty_cycle_right_backwards = 0;
    } else {
        duty_cycle_right_backwards = -duty_cycle_right;
        duty_cycle_right_forwards = 0;
    }

    if (duty_cycle_left > 0) {
        duty_cycle_left_forwards = duty_cycle_left;
        duty_cycle_left_backwards = 0;
    } else {
        duty_cycle_left_backwards = -duty_cycle_left;
        duty_cycle_left_forwards = 0;
    }
    
    // writes duty to the pins on the h bridge ( unchanged by isha )
    pwm_duty_set(pwm1, PWM_DUTY_DIVISOR(PWM_FREQ_HZ, duty_cycle_left_forwards));
    pwm_duty_set(pwm2, PWM_DUTY_DIVISOR(PWM_FREQ_HZ, duty_cycle_right_forwards));
    pwm_duty_set(pwm3, PWM_DUTY_DIVISOR(PWM_FREQ_HZ, duty_cycle_left_backwards));
    pwm_duty_set(pwm4, PWM_DUTY_DIVISOR(PWM_FREQ_HZ, duty_cycle_right_backwards));
}

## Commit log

2024-02-21 started on the power supply ciruits
    [Basic_with_power.PrjPcb, MCU.SchDoc, Power_Supply.SchDoc]
2024-02-21 Added fuse and reverse polatrity protection
    [MCU.SchDoc, Power_Supply.SchDoc]
2024-02-21 Started on buck converter
    [Power_Supply.SchDoc]
2024-02-22 Finished Buck converter
    [Power_Supply.SchDoc]
2024-02-22 Added all improvements from tutorial
    [MCU.SchDoc, Power_Supply.SchDoc]
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2024-02-24 Added questions ready for periferals
    [MCU.SchDoc, Power_Supply.SchDoc]
2024-02-24 Added Radio and tidied up
    [Basic_with_power.PrjPcb, MCU.SchDoc, Peripherals.SchDoc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]
2024-02-25 Ready for merge
    [MCU.SchDoc, Peripherals.SchDoc, Power_Supply.SchDoc]
2024-02-25 Added racer and hat projects
    [Hat.PrjPcb, MCU.SchDoc, Peripherals.SchDoc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]
2024-02-25 Hat schematic with small changes to be made
    [Hat.PrjPcb, MCU.SchDoc, Peripherals.SchDoc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]
2024-02-26 LED added to racer
    [MCU.SchDoc, Peripherals.SchDoc]
2024-02-26 update changes
    [MCU.SchDoc, Peripherals.SchDoc]
2024-02-26 added bump sensor, led strip power, compelted H bridge
    [MCU.SchDoc, Peripherals.SchDoc, Power_Supply.SchDoc]
2024-02-26 Formatting changes
    [MCU.SchDoc, Peripherals.SchDoc, Power_Supply.SchDoc]
2024-02-26 Add connections to MCU
    [MCU.SchDoc, Peripherals.SchDoc]
2024-02-26 Wacky racer review
    [MCU.SchDoc, Peripherals.SchDoc, Power_Supply.SchDoc]
2024-02-27 Updated Basic
    [MCU.SchDoc, Power_Supply.SchDoc]
2024-02-27 Hat schematic
    [MCU.SchDoc, Peripherals.SchDoc, Power_Supply.SchDoc]
2024-02-27 Hat ready for checking
    [MCU.SchDoc, Peripherals.SchDoc, Power_Supply.SchDoc]
2024-02-27 With anotations and checklist checked
    [MCU.SchDoc, Peripherals.SchDoc, Power_Supply.SchDoc]
2024-02-27 added test points to H bridge
    [Peripherals.SchDoc]
2024-03-03 Added MOSFETs for actuators
    [MCU.SchDoc, Peripherals.SchDoc]
2024-03-03 Ready for schematic inspection
    [Hat.PrjPcb, MCU.SchDoc, Peripherals.SchDoc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]
2024-03-05 Added comments from review and changed some headers
    [Hat.PrjPcb, Hat_PCB.PcbDoc, MCU.SchDoc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]
2024-03-05 Added designators
    [MCU.SchDoc, Peripherals.SchDoc, Power_Supply.SchDoc]
2024-03-06 Started PCB design
    [Hat.PrjPcb, Hat_PCB.PcbDoc]
2024-03-06 PCB started
    [Hat_PCB.PcbDoc]
2024-03-06 PCB grouping related components
    [Hat_PCB.PcbDoc]
2024-03-07 Moved Components back to the correct positions
    [Hat.PrjPcb, Hat_PCB.PcbDoc, MCU.SchDoc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]
2024-03-07 Most components on board
    [Hat_PCB.PcbDoc, MCU.SchDoc, Peripherals.SchDoc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]
2024-03-09 Aligned Components and regioned power plane
    [Hat_PCB.PcbDoc]
2024-03-09 Seperated Power Planes
    [Hat_PCB.PcbDoc]
2024-03-10 Added copper cut outs for radio
    [Hat_PCB.PcbDoc]
2024-03-10 Completed most of the power traces and some signaling
    [Hat.PrjPcb, Hat_PCB.PcbDoc]
2024-03-10 car board setup
    [Car_PCB.PcbDoc, MCU.SchDoc, Peripherals.SchDoc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]
2024-03-11 component grouping for racer
    [Car_PCB.PcbDoc]
2024-03-11 grouping all components, MCU pg, bump sensor, & LED PCB
    [Car_PCB.PcbDoc]
2024-03-11 Routed some signalling and added pin labels to headers
    [Hat_PCB.PcbDoc]
2024-03-12 Revert "Routed some signalling and added pin labels to headers"
    This reverts commit 87860473c56f12c7f14cacdee697f1a5c320cc1d.
    [Hat_PCB.PcbDoc]
2024-03-12 Hat PCB routing, buzzer, test points
    [Hat_PCB.PcbDoc, Peripherals.SchDoc]
2024-03-12 Most tracing done
    [Hat_PCB.PcbDoc]
2024-03-12 Changed MCU pins around
    [Hat_PCB.PcbDoc, MCU.SchDoc]
2024-03-12 Acc Tracing and silkscreen tidy
    [Hat_PCB.PcbDoc]
2024-03-12 Fixed stuff up for lab check
    [Hat_PCB.PcbDoc, Peripherals.SchDoc]
2024-03-12 Racer changes/git test
    [Car_PCB.PcbDoc]
2024-03-13 Cut out plane for radio
    [Car_PCB.PcbDoc]
2024-03-13 Layed out Motor Drivers
    [Car_PCB.PcbDoc]
2024-03-13 Removed joystick and re wired buck
    [Hat_PCB.PcbDoc, MCU.SchDoc, Peripherals.SchDoc]
2024-03-13 Buck converter placed
    [Car_PCB.PcbDoc, Power_Supply.SchDoc]
2024-03-13 Radio Voltage regulator placement
    [Car_PCB.PcbDoc]
2024-03-13 Actuators and regulators
    [Car_PCB.PcbDoc]
2024-03-13 Placing test points
    [Car_PCB.PcbDoc, MCU.SchDoc, Peripherals.SchDoc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]
2024-03-13 Racer components Placed
    [Car_PCB.PcbDoc]
2024-03-13 Retraced most of Hat PCB
    [Hat_PCB.PcbDoc]
2024-03-13 Most design rules taken care of
    [Hat_PCB.PcbDoc, MCU.SchDoc]
2024-03-14 Moved one trace
    [Hat_PCB.PcbDoc]
2024-03-14 Traced one Vreg
    [Car_PCB.PcbDoc]
2024-03-14 Adding Power plane partitions
    [Car_PCB.PcbDoc]
2024-03-14 Checked over Hat PCB and added connector/switch labels
    [Hat_PCB.PcbDoc]
2024-03-15 Added vias to v reg
    [Car_PCB.PcbDoc]
2024-03-15 tracers for crystal
    [Car_PCB.PcbDoc]
2024-03-15 Tracers added to decoup
    [Car_PCB.PcbDoc]
2024-03-15 Added additional tacers
    [Car_PCB.PcbDoc]
2024-03-15 Tented MCU vias and moved radio switches
    [Hat_PCB.PcbDoc, Peripherals.SchDoc]
2024-03-15 Radio tracers
    [Car_PCB.PcbDoc]
2024-03-15 Buck converter traces
    [Car_PCB.PcbDoc, Hat_PCB.PcbDoc]
2024-03-16 Racer traces
    [Car_PCB.PcbDoc, MCU.SchDoc]
2024-03-16 Motor driver traces
    [Car_PCB.PcbDoc, MCU.SchDoc]
2024-03-16 Actuator traces
    [Car_PCB.PcbDoc]
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2024-03-17 everything done except actuators
    [Car_PCB.PcbDoc, Peripherals.SchDoc]
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2024-03-17 Added Group name to PCB
    [Hat_PCB.PcbDoc]
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2024-03-17 Complete first routing for Racer
    [Car_PCB.PcbDoc]
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2024-03-18 Design Rules resolved
    [Car_PCB.PcbDoc]
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2024-03-18 Last changes for submittion
    [Car_PCB.PcbDoc, Peripherals.SchDoc]
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2024-04-30 added title blocks and includes to buzzer file
    [buzzer.c]
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2024-05-05 Tested motors not working 3 hours - Conclusion: Power supply was plugged into the wrong channel
    [motor_driver.c, target.h]
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2024-05-11 Fixed control limits and direction
    [communications.c, control.c]
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2024-05-17 Added buzzer but it is very quiet
    [buzzer.c, communications.c, hat.c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]
2024-05-19 Buzzer song running radio set to only enable
    [buzzer.c, communications.c, control.c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]
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
